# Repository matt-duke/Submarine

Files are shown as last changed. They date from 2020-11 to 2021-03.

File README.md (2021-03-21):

# Underwater ROV

## Motivation
The inspiration for this project was born on a sunny summer day on Skeleton Lake in Ontario, Canada. This lake is thought to be formed by a meteorite impact about 800 million years ago, followed by several periods of glaciation. This origin story, combined with the lake's crystal clear spring fed water, has resulted in clearly visible incredible underwater topography. However, only a very small portion can be seen from the waters surface, leaving acres of interesting glacial aftermath, submarine rock cliffs and (possibly) optimistic plant life hidden from view and left to the imagination.

<figure>
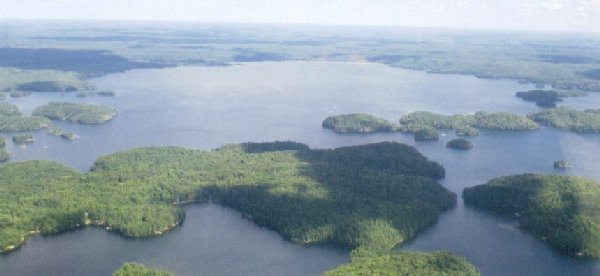
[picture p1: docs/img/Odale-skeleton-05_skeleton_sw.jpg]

<figcaption><p align=center>Aerial view of the west side of Skeleton Lake</p></figcaption>
</figure>

The intent of this project has been part practical outcome and part learning experience. So far, the learning portion has been extremely valuable, with many iterations, over-complications and replacements. However, a working prototype is planned for the spring of 2021.

## System Overview
The ROV consists of 3 sperate processors with specific functions dedicated to each. The main processor card (MPC) inside the submarine handles high level monitoring and control tasks, including a database server. It is connected by a CAT5 link to the auxillary processor card (APC), which is on the water's surface and acts as the human to machine interface. This device is intended to receive user commands and send them to the MPC, while displaying critical information with minimal delay.
<figure>
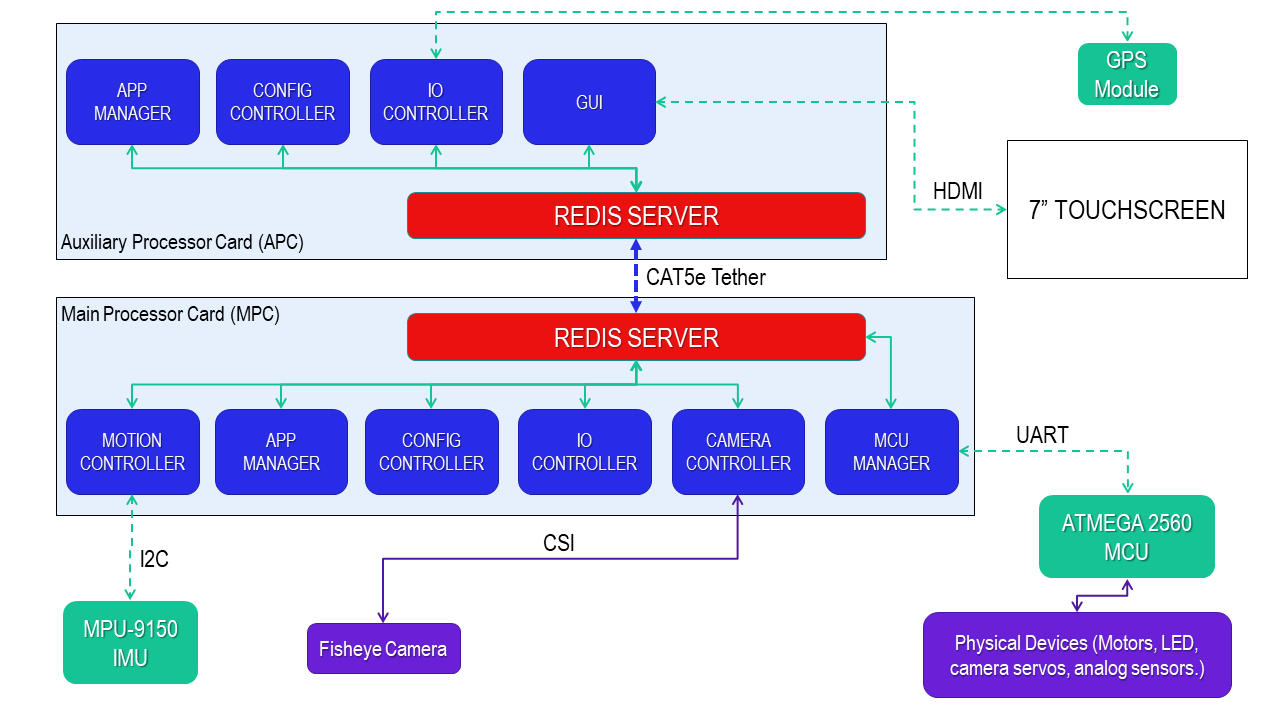
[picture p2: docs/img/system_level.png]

<figcaption><p align=center>System level block diagram</p></figcaption>
</figure>
Because low latency is critical in this application, inter-process communication is accomplished using a Redis server. It acts as an in memory variable cache, with the added ability to act as a message broker. The main redis server lives on the MPC inside the submarine, with a synchronized redis server on the APC acting as a forwarder.

### Hardware

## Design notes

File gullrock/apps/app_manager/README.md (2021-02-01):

# Application Manager

## Overview
This application starts and monitors other apps to watch for faults and crashes. It also starts thirdparty apps such as redis-server. As the main entrypoint for submarine software, it should be run at startup and launch applications in the correct sequence.

## Redis Details
Device code is either `mpc` or `apc`.
### Keys:
`<device_code>_app_manager:` Current app status
### Publishers:
N/A
### Subscriptions:
`<device_code>_app_manager.transition`: Request transition to given state ID
## Requirements
```
    logger
    hiredis
    pthread
    event
    event_pthreads
```

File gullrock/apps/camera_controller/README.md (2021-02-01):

# Camera Controller

## Overview
This application handles camera specific functionality. It controls the RaspiCam and a gstream server to send video to the APC using IP level protocols. This method is the best I've found for low latency, high quality digital video streaming, and allows for a very fine level of control.

## Redis Details
Device code is either `mpc` or `apc`.
### Keys:
`<device_code>_camera_controller`: Current app status
`cam_status`: Output of vcgencmd camera status (supported and detected)
### Publishers:
N/A
### Subscriptions:
`<device_code>_camera_controller.transition`: Request transition to given state ID
`start_camera_server`: Initialize camera server (gstream) to send video to APC
`stop_camera_server`: Stop camera stream
## Requirements
```
    logger
    hiredis
    pthread
    event
    event_pthreads
```

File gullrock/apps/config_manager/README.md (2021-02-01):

# Config Manager

## Overview
This application is used to detect software validity and iniiliaze common variables from configuration files. It is heavily involved in the firmware update procedure by reading app CRC values and comparing to expected values. This feature is less critical for development and can be disabled or ignored.

## Redis Details
Device code is either `mpc` or `apc`.
### Keys:
`<device_code>_config_manager`: Current app status
### Publishers:
N/A
### Subscriptions:
`<device_code>_config_manager.transition`: Request transition to given state ID
## Requirements
```
    logger
    hiredis
    pthread
    event
    event_pthreads
```

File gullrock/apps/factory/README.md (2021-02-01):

# Factory

## Overview
Apps for use by the "factory" (me) and not for use on "production" hardware. Examples include sensor calibration apps that need to be run on target hardware.

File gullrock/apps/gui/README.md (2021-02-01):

## GUI Interface

## Overview
This Python based GUI is meant to be used from a device on the water's surface, connected by ethernet tether to the ROV. It is designed to be used on the APC, which is a Raspberry Pi touchscreen tablet meant to act as a cheap, portable and replacable alternative to and laptop or tablet.

This GUi is relatively simple and has 3 tasks:
- Read and display data from a Redis database
- Send commands to the ROV using Redis PUBSUB
- Display video by connecting to the GStream server

GUI input is meant to come from a touchscreen or (preferably) an off-the-shelf USB game controller.

## Redis Details
### Keys:
`qt5_gui_status`: Current app status
### Publishers:
`set.io.m1_speed`
`set.io.m2_speed`
`set.io.cam_pitch`
`set.io.cam_yaw`
`set.io.headlight`
### Subscriptions:
`mcu_refresh`: ? Uncertain whether to use polling or notifications for GUI refresh
## Requirements
`python3-gi python3-gi-cairo gir1.2-gtk-3.0`: PyGObject support on Debian based distro
See requirements.txt for PIP packages

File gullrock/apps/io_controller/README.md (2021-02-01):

# IO Controller

## Overview
Manages all functionality regarding the MPC or APc and its physical surroudnings or hardware status. Used mainly for gathering and updating the Redis database with sensor data, including CPU temperature and IMU sensor results.

The main loop in this app should be very fast to minimize data lag.

## Redis Details
Device code is either `mpc` or `apc`.
### Keys:
`<device_code>_io_controller`: Current app status
`accel_x`: X-wise acceleration
`accel_y`: Y-wise acceleration
`accel_z`: Z-wise acceleration (including gravity)
`<device_code>_cpu_temp`: vcgencmd reported CPU temperature
`<device_code>_volts`: vcgencmd reported core voltage
`<device_code>_cpu_idle`: CPU idle time since last startup
`<device_code>_load_avg_1min`: CPU load avg over previous 1min (total, not per core)
`<device_code>_load_avg_5min`: CPU load avg over previous 5min (total, not per core)
`<device_code>_load_avg_15min`: CPU load avg over previous 15min (total, not per core)
`<device_code>_under_volt`: vcgencmd CPU undervolt detected
`<device_code>_freq_cap`: vcgencmd CPU frequency capped
`<device_code>_throttled`: vcgencmd CPU currently throttled
`<device_code>_soft_temp_limit`: vcgencmd CPU soft temp limit reached
### Publishers:
N/A
### Subscriptions:
`<device_code>_io_controller.transition`: Request transition to given state ID
## Requirements
```
    logger
    hiredis
    pthread
    event
    event_pthreads
    mpu9150
```

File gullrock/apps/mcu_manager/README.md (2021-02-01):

# MCU Manager

## Overview
The MCU manager acts as a bridge between the Rasberry Pi based MPC and the ATmega2560 based MCU. A serial connection between the two devices uses the HDLC message format to form data packets, which includes start and stop bytes plus a CRC embeded in the payload. To simplify the protocol, the MCU acts as a slave, and only responds to messages following a request for data from the MPC. 
This app needs relatively high speed to update the Redis server in near real-time.

## Redis Details
Device code is either `mpc` or `apc`.
### Keys:
`<device_code>_mcu_manager`: Current app status
`m1_speed`: Left motor speed (0-255)
`m2_speed`: Right motor speed (0-255)
`m1_curr`: Left motor current in volts
`m2_curr`: Right motor current in volts
`mcu_state`: Internal state reported by MCU firmware
`water temp`: Submarine water temperature (sensor onboard)
`total_current`: Total current draw from submarine batteries
### Publishers:
N/A
### Subscriptions:
`<device_code>_mcu_manager.transition`: Request transition to given state ID
`set.io.*`: Listens to requests to set MCU settings such as `m1_speed` or `cam_yaw`

## Requirements
```
    logger
    hiredis
    pthread
    event
    event_pthreads
    serialport
    minihdlc
```

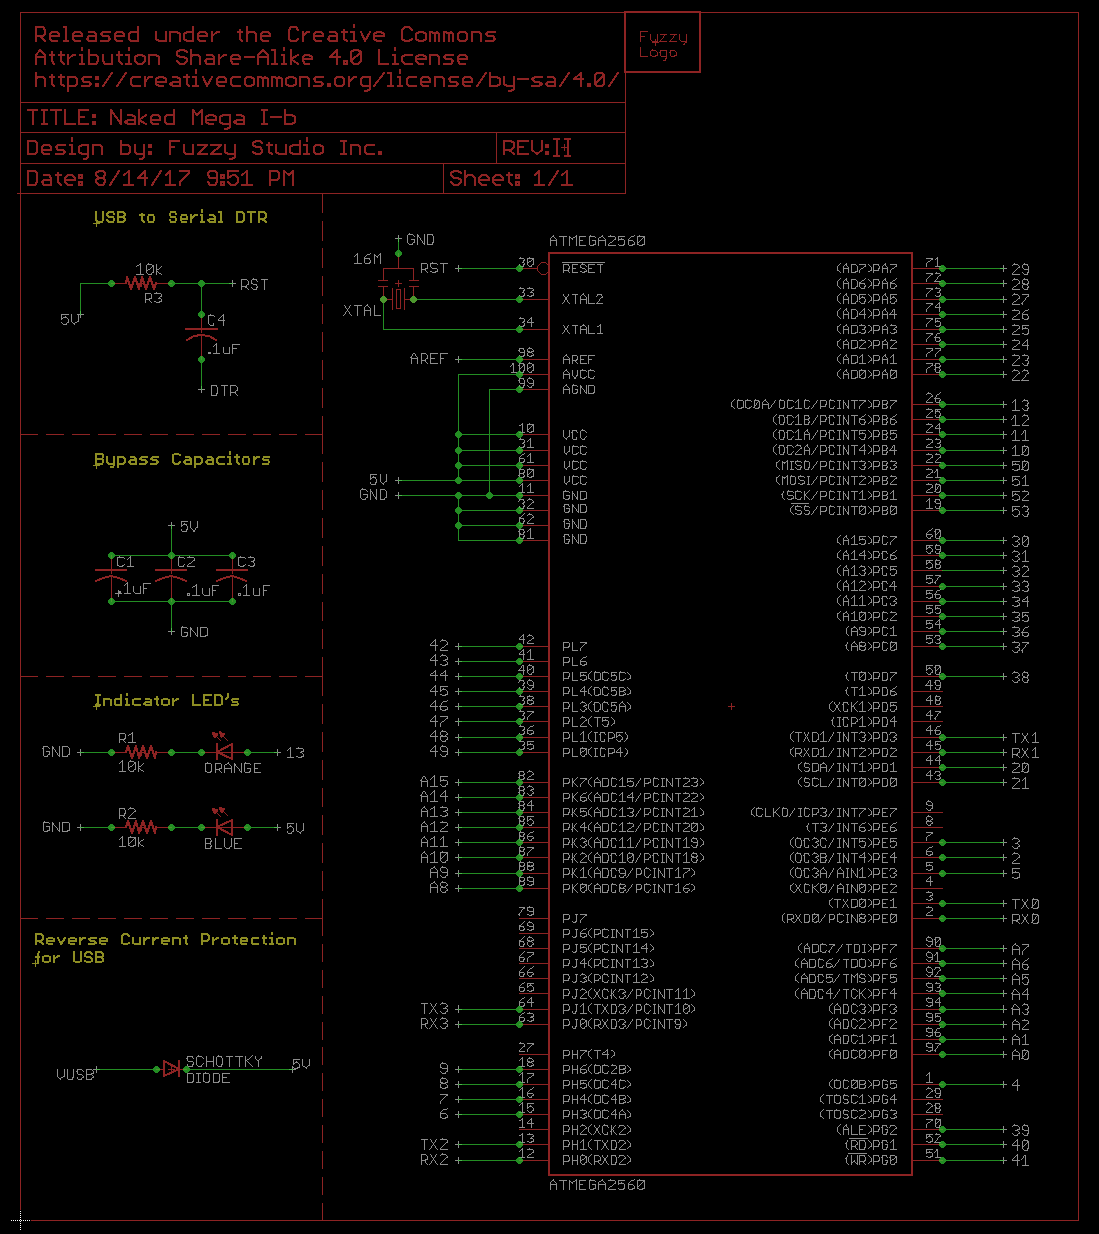
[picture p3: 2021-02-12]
CAD/MPC/Fuzzy-Naked-Mega-master/Revision I-b/Schematic.png

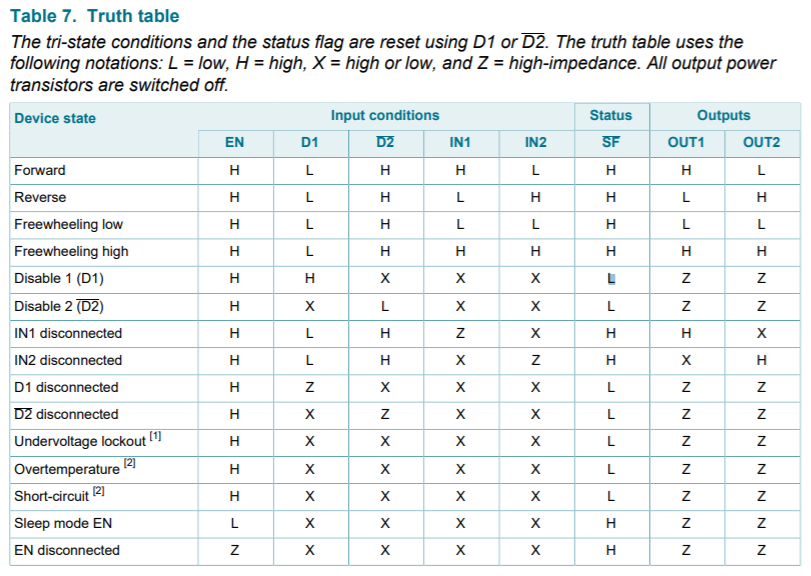
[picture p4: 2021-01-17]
docs/MC33926 truth table.PNG

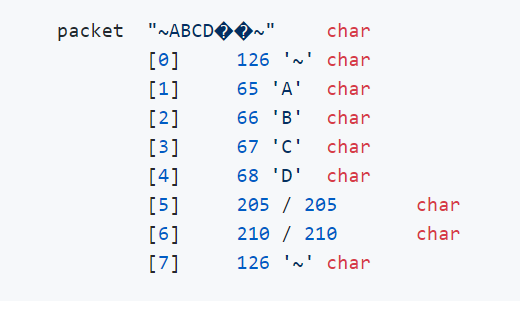
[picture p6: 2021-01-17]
docs/packet framing hdlc.PNG

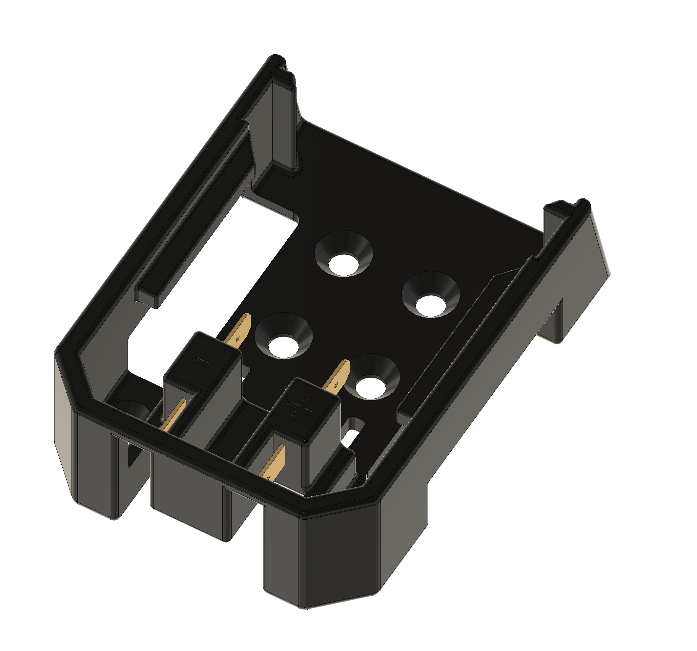
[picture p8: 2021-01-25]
CAD/V3/milwaukee-m18-battery-adapter-connector-dock-holder-mount-injection-molded-1.snapshot.3/Screen Shot 2020-12-06 at 12.32.36 PM.png

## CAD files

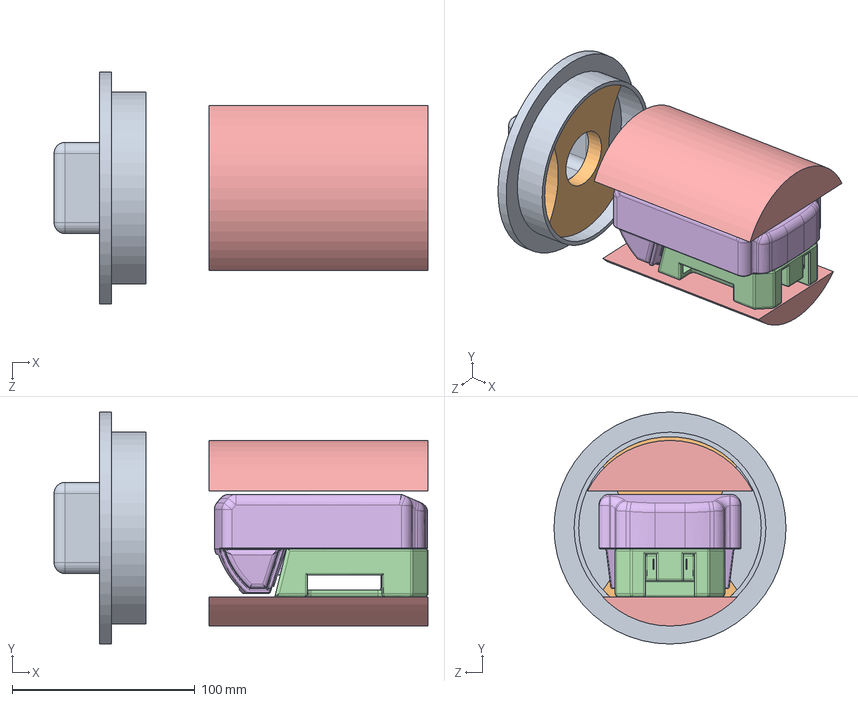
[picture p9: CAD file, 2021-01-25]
CAD/V3/Assem1.SLDASM
204.8 x 127.0 x 127.0 mm
Frame.step
battery_adaptor_mount
Milwaukee M18 Red Lithium Battery.step

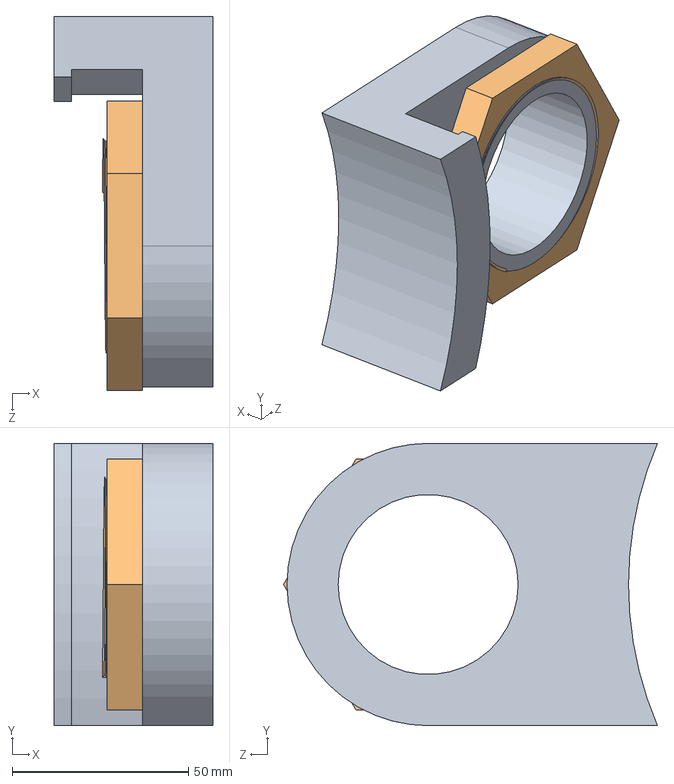
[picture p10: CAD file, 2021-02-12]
CAD/assem_led.SLDASM
45.0 x 80.0 x 106.0 mm
led_mount
bolt

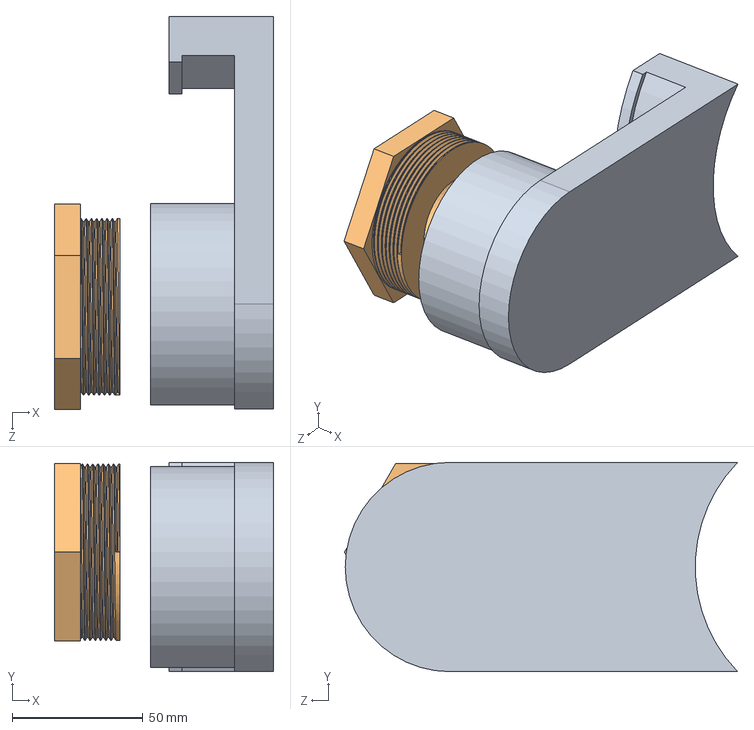
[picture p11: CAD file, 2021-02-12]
CAD/assem_motor.SLDASM
83.7 x 80.0 x 150.3 mm
motor_mount
bolt_motor

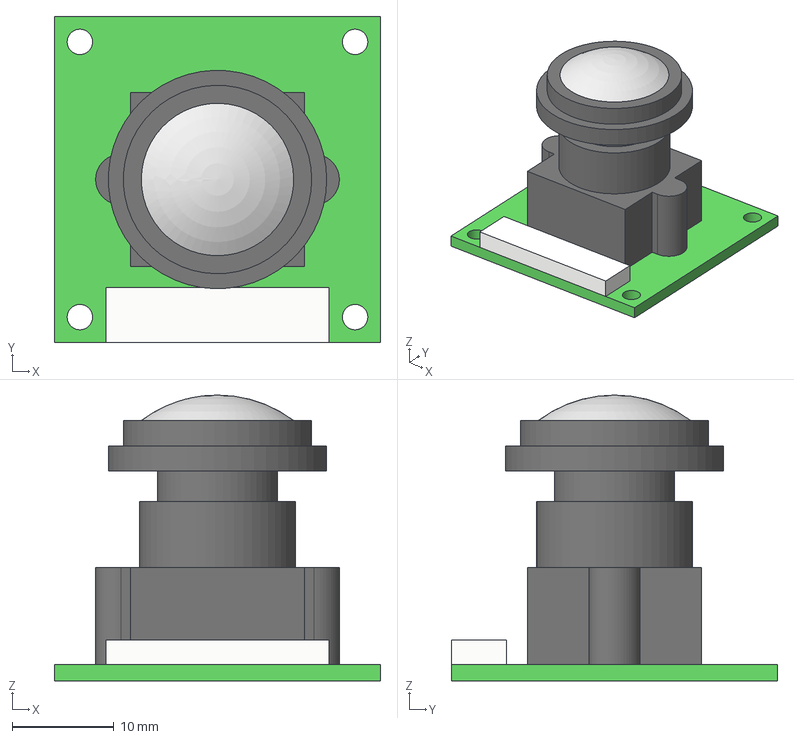
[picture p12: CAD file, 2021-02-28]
CAD/PiCam_WideAngle v2.step
32.1 x 32.1 x 28.2 mm
Lens
Connector
Lense frame
PCB
Camera Body

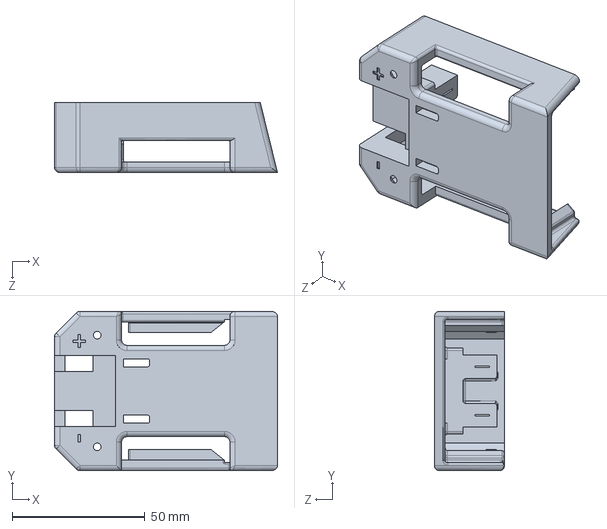
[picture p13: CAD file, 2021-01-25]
CAD/V3/battery_mount_2.SLDPRT
83.9 x 60.0 x 26.4 mm

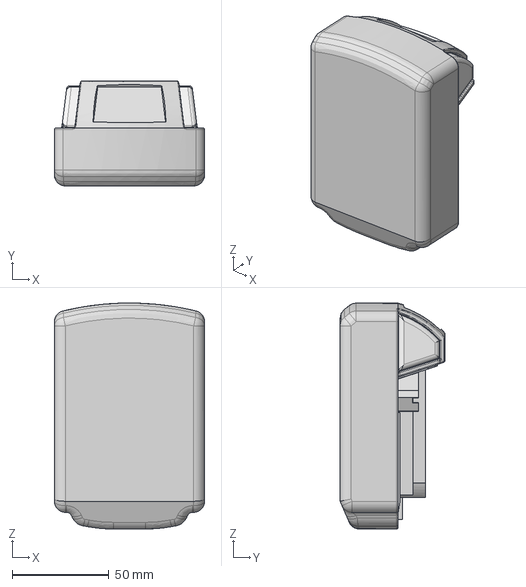
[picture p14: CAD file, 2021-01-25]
CAD/V3/milwaukee-m18-battery-1.snapshot.3/Milwaukee M18 Red Lithium Battery.step
77.7 x 54.2 x 116.8 mm

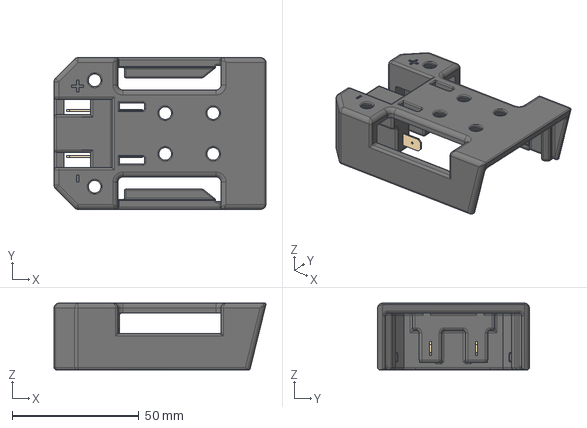
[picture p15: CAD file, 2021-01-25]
CAD/V3/milwaukee-m18-battery-adapter-connector-dock-holder-mount-injection-molded-1.snapshot.3/M18 battery mount.step
83.7 x 60.0 x 26.4 mm
Contacts
Frame

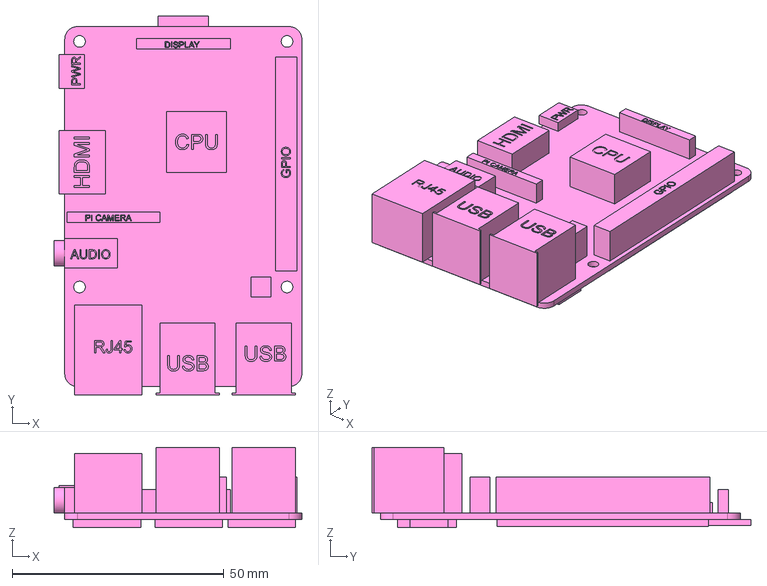
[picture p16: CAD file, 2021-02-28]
CAD/Raspberry pi 3B+ model v10.step
58.5 x 89.5 x 19.0 mm

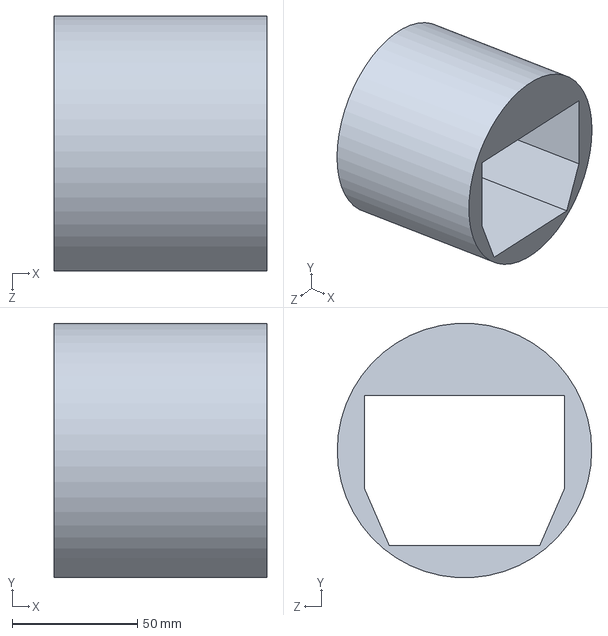
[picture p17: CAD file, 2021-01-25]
CAD/V3/battery_adaptor_mount.SLDPRT
85.0 x 101.4 x 101.6 mm

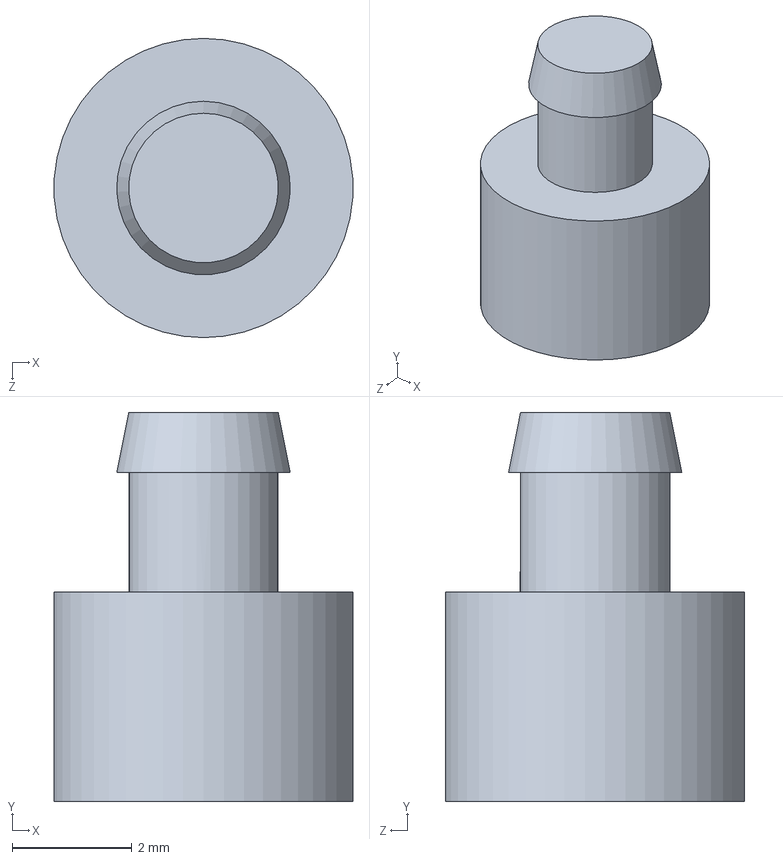
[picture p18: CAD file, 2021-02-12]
CAD/spacer_board.SLDPRT
4.99 x 6.50 x 5.00 mm

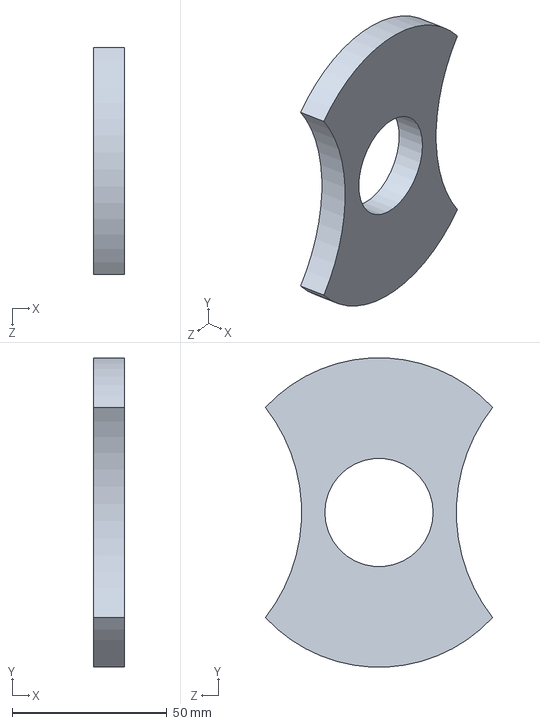
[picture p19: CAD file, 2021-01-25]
CAD/V3/PLA_cap_insert.SLDPRT
10.0 x 99.9 x 73.4 mm

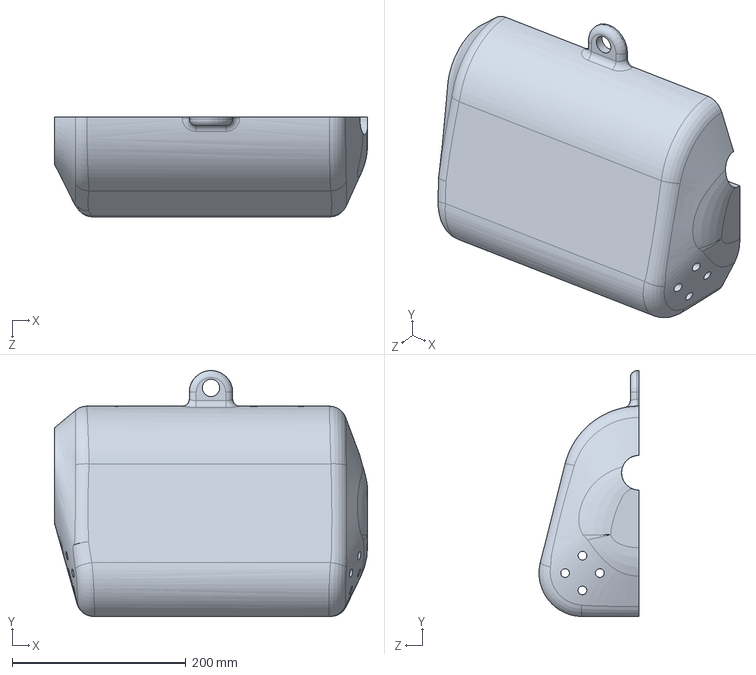
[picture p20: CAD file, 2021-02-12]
CAD/sub3.SLDPRT
360.0 x 283.0 x 115.0 mm

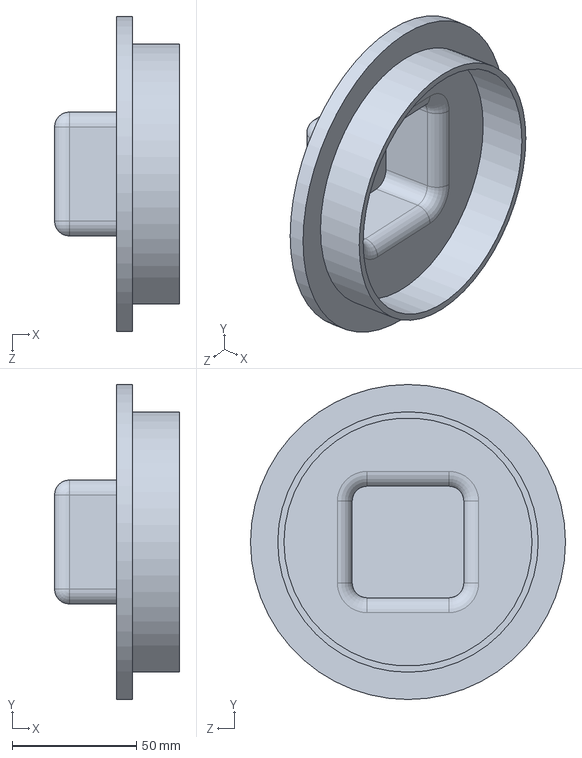
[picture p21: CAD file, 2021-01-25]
CAD/V3/4in_ABS_cap.SLDPRT
50.4 x 127.0 x 127.0 mm

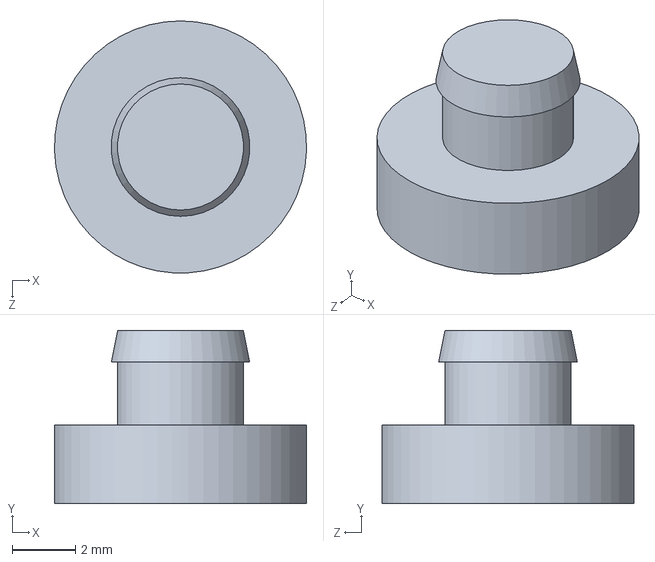
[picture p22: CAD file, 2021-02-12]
CAD/spacer_front.SLDPRT
8.00 x 5.50 x 8.00 mm

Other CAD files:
CAD/spacer_rpi.SLDPRT
CAD/spacer_motor.SLDPRT
CAD/sub_final.SLDPRT
CAD/mount template.SLDPRT
CAD/V3/milwaukee-m18-battery-1.snapshot.3/Milwaukee M18 Red Lithium battery.f3d
CAD/V3/milwaukee-m18-battery-adapter-connector-dock-holder-mount-injection-molded-1.snapshot.3/M18 battery mount.SLDPRT
CAD/board_standoff.SLDPRT
CAD/bolt.SLDPRT
CAD/bolt_led.SLDPRT
CAD/bolt_motor.SLDPRT
CAD/cam_mount.SLDPRT
CAD/controller.SLDPRT
CAD/controller_rounded.SLDPRT
CAD/led_mount.SLDPRT
CAD/light_mount.SLDPRT
CAD/motor_mount.SLDPRT
CAD/mount.SLDPRT
CAD/part_mount_template.SLDPRT
CAD/servo_mnt_2.SLDPRT
CAD/spacer_ard.SLDPRT
CAD/spacer_ethernet.SLDPRT
CAD/sub1.SLDPRT
CAD/sub2.SLDPRT

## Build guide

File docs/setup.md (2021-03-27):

# Building
## Cross Compiling
http://amgaera.github.io/blog/2014/04/10/cross-compiling-for-raspberry-pi-on-64-bit-linux/
https://stackoverflow.com/questions/19162072/how-to-install-the-raspberry-pi-cross-compiler-on-my-linux-host-machine/58559140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
https://stackoverflow.com/questions/5971921/building-a-library-using-autotools-from-cmake
https://stackoverflow.com/questions/19162072/how-to-install-the-raspberry-pi-cross-compiler-on-my-linux-host-machine
https://stackoverflow.com/questions/33559884/fatal-error-bits-types-h-file-not-found
https://stackoverflow.com/questions/11471722/libstdc-so-6-cannot-open-shared-object-file-no-such-file-or-directory

autoreconf
libtool
gcc
g++

## Generating image for Raspberry Pi
https://github.com/zeromq/czmq/tree/master/builds/rpi

# Dependecies
## GSTREAMER
gir1.2-gst-plugins-base-1.0 -- for GstVideo (not needed?)

gstreamer1.0-libav

## REDIS
wget http://download.redis.io/redis-stable.tar.gz
tar xvzf redis-stable.tar.gz
cd redis-stable
make

git clone git://git.drogon.net/wiringPi
$ cd wiringPi
$ ./build

## REDIS C LIBRARY
hiredis-vip
make -> generates libhiredis_vip.so
copy to /usr/lib
update using sudo ldconfig
check with sudo ldconfig -p | grep redis

## SERIAL LIBRARY
git clone https://github.com/sigrokproject/libserialport.git
install dh-autoreconf
run autogen.sh, then configure.sh
make install
ldconfig

## GST_RPICAM
#https://github.com/thaytan/gst-rpicamsrc/
sudo apt install libgstreamer1.0-dev libgstreamer-plugins-base1.0-dev
git clone https://github.com/thaytan/gst-rpicamsrc.git
cd gst-rpicamsrc
./autogen.sh
make
sudo make install

## Disable BT to use UART (PL011)
https://scribles.net/disabling-bluetooth-on-raspberry-pi/
https://www.raspberrypi.org/documentation/configuration/uart.md

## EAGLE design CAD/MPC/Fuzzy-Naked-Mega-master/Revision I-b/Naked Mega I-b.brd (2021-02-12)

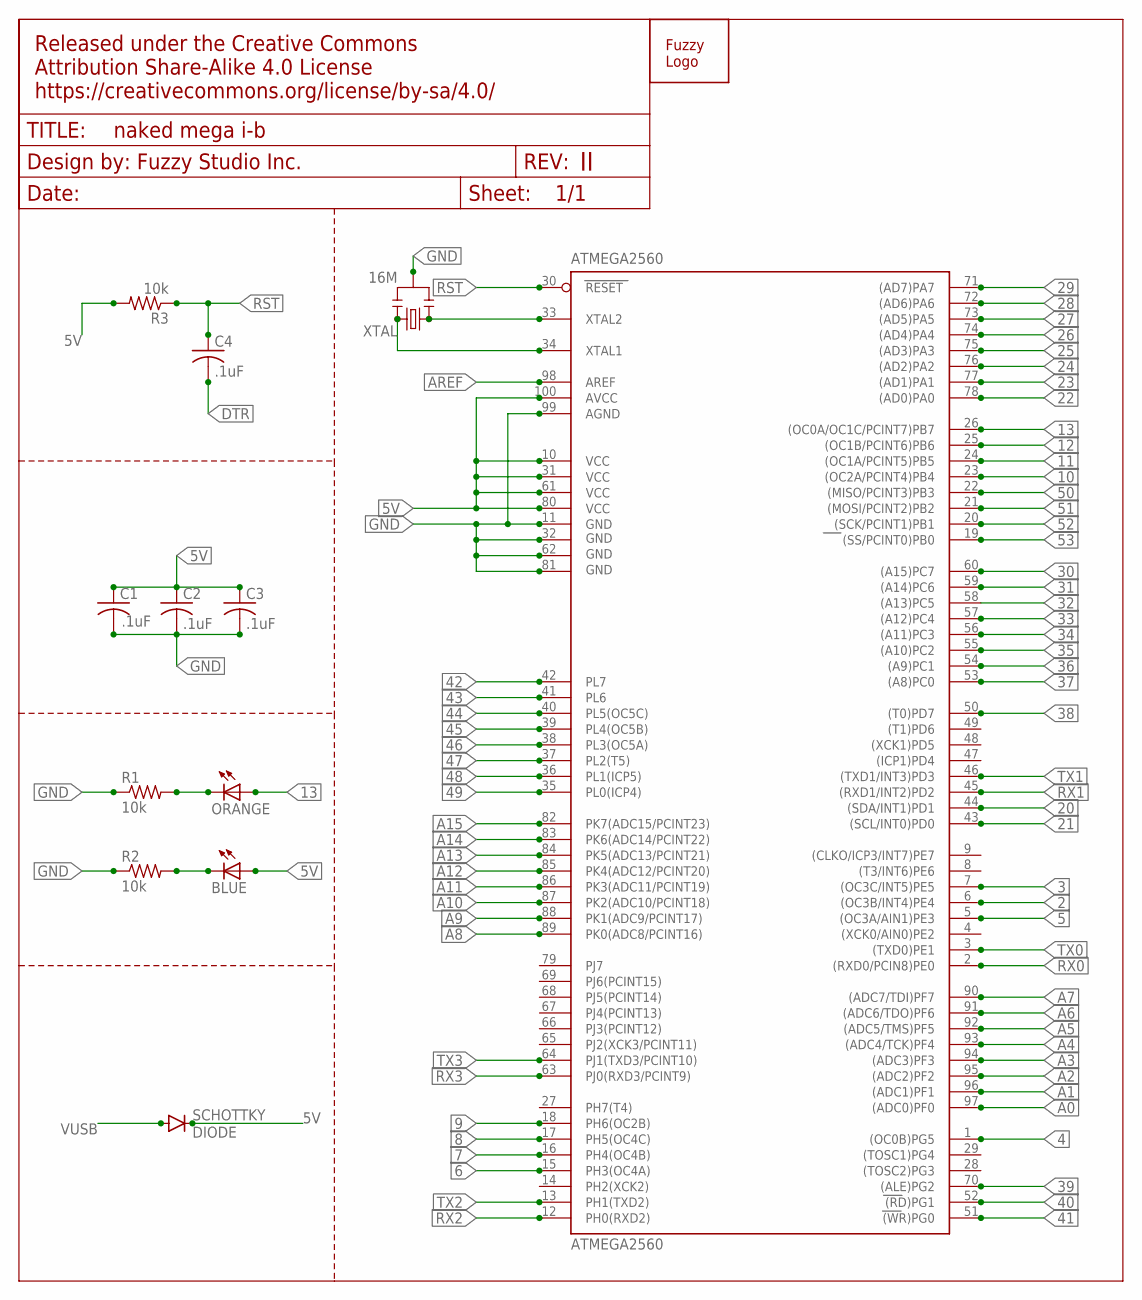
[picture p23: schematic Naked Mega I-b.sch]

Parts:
ATMEGA2560: ATMEGA2560; TQFP100
BLUE: L; SMD-0805-LED
C1: CAPACITOR-SMD-0805; SMD-0805
C2, C3, C4: .1uF; SMD-0805
ORANGE: L; SMD-0805-LED
R1, R2, R3: 10k; SMD-0805
SCHOTTKY: DIODE; SOD-323
U$1: LOGO; LOGO-S
U$3: DOCFRAME; CREATIVECOMMONS
XTAL: 16M; RESONATOR

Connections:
2: ATMEGA2560.6 ((OC3B/INT4)PE4)
3: ATMEGA2560.7 ((OC3C/INT5)PE5)
4: ATMEGA2560.1 ((OC0B)PG5)
5: ATMEGA2560.5 ((OC3A/AIN1)PE3)
5V: ATMEGA2560.10 (VCC), ATMEGA2560.31 (VCC1), ATMEGA2560.61 (VCC2), ATMEGA2560.80 (VCC3), ATMEGA2560.100 (AVCC), BLUE.1 (A), C1.1, C2.1, C3.1, R3.2, SCHOTTKY.C
6: ATMEGA2560.15 (PH3(OC4A))
7: ATMEGA2560.16 (PH4(OC4B))
8: ATMEGA2560.17 (PH5(OC4C))
9: ATMEGA2560.18 (PH6(OC2B))
10: ATMEGA2560.23 ((OC2A/PCINT4)PB4)
11: ATMEGA2560.24 ((OC1A/PCINT5)PB5)
12: ATMEGA2560.25 ((OC1B/PCINT6)PB6)
13: ATMEGA2560.26 ((OC0A/OC1C/PCINT7)PB7), ORANGE.1 (A)
20: ATMEGA2560.44 ((SDA/INT1)PD1)
21: ATMEGA2560.43 ((SCL/INT0)PD0)
22: ATMEGA2560.78 ((AD0)PA0)
23: ATMEGA2560.77 ((AD1)PA1)
24: ATMEGA2560.76 ((AD2)PA2)
25: ATMEGA2560.75 ((AD3)PA3)
26: ATMEGA2560.74 ((AD4)PA4)
27: ATMEGA2560.73 ((AD5)PA5)
28: ATMEGA2560.72 ((AD6)PA6)
29: ATMEGA2560.71 ((AD7)PA7)
30: ATMEGA2560.60 ((A15)PC7)
31: ATMEGA2560.59 ((A14)PC6)
32: ATMEGA2560.58 ((A13)PC5)
33: ATMEGA2560.57 ((A12)PC4)
34: ATMEGA2560.56 ((A11)PC3)
35: ATMEGA2560.55 ((A10)PC2)
36: ATMEGA2560.54 ((A9)PC1)
37: ATMEGA2560.53 ((A8)PC0)
38: ATMEGA2560.50 ((T0)PD7)
39: ATMEGA2560.70 ((ALE)PG2)
40: ATMEGA2560.52 ((RD)PG1)
41: ATMEGA2560.51 ((WR)PG0)
42: ATMEGA2560.42 (PL7)
43: ATMEGA2560.41 (PL6)
44: ATMEGA2560.40 (PL5(OC5C))
45: ATMEGA2560.39 (PL4(OC5B))
46: ATMEGA2560.38 (PL3(OC5A))
47: ATMEGA2560.37 (PL2(T5))
48: ATMEGA2560.36 (PL1(ICP5))
49: ATMEGA2560.35 (PL0(ICP4))
50: ATMEGA2560.22 ((MISO/PCINT3)PB3)
51: ATMEGA2560.21 ((MOSI/PCINT2)PB2)
52: ATMEGA2560.20 ((SCK/PCINT1)PB1)
53: ATMEGA2560.19 ((SS/PCINT0)PB0)
A0: ATMEGA2560.97 ((ADC0)PF0)
A1: ATMEGA2560.96 ((ADC1)PF1)
A2: ATMEGA2560.95 ((ADC2)PF2)
A3: ATMEGA2560.94 ((ADC3)PF3)
A4: ATMEGA2560.93 ((ADC4/TCK)PF4)
A5: ATMEGA2560.92 ((ADC5/TMS)PF5)
A6: ATMEGA2560.91 ((ADC6/TDO)PF6)
A7: ATMEGA2560.90 ((ADC7/TDI)PF7)
A8: ATMEGA2560.89 (PK0(ADC8/PCINT16))
A9: ATMEGA2560.88 (PK1(ADC9/PCINT17))
A10: ATMEGA2560.87 (PK2(ADC10/PCINT18))
A11: ATMEGA2560.86 (PK3(ADC11/PCINT19))
A12: ATMEGA2560.85 (PK4(ADC12/PCINT20))
A13: ATMEGA2560.84 (PK5(ADC13/PCINT21))
A14: ATMEGA2560.83 (PK6(ADC14/PCINT22))
A15: ATMEGA2560.82 (PK7(ADC15/PCINT23))
AREF: ATMEGA2560.98 (AREF)
DTR: C4.2
GND: ATMEGA2560.11 (GND), ATMEGA2560.32 (GND1), ATMEGA2560.62 (GND2), ATMEGA2560.81 (GND3), ATMEGA2560.99 (AGND), C1.2, C2.2, C3.2, R1.1, R2.1, XTAL.2
unnamed: ATMEGA2560.34 (XTAL1), XTAL.3
unnamed: ATMEGA2560.33 (XTAL2), XTAL.1
unnamed: ORANGE.2 (C), R1.2
unnamed: BLUE.2 (C), R2.2
RST: ATMEGA2560.30 (RESET), C4.1, R3.1
RX0: ATMEGA2560.2 ((RXD0/PCIN8)PE0)
RX1: ATMEGA2560.45 ((RXD1/INT2)PD2)
RX2: ATMEGA2560.12 (PH0(RXD2))
RX3: ATMEGA2560.63 (PJ0(RXD3/PCINT9))
TX0: ATMEGA2560.3 ((TXD0)PE1)
TX1: ATMEGA2560.46 ((TXD1/INT3)PD3)
TX2: ATMEGA2560.13 (PH1(TXD2))
TX3: ATMEGA2560.64 (PJ1(TXD3/PCINT10))
VUSB: SCHOTTKY.A

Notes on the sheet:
.1uF

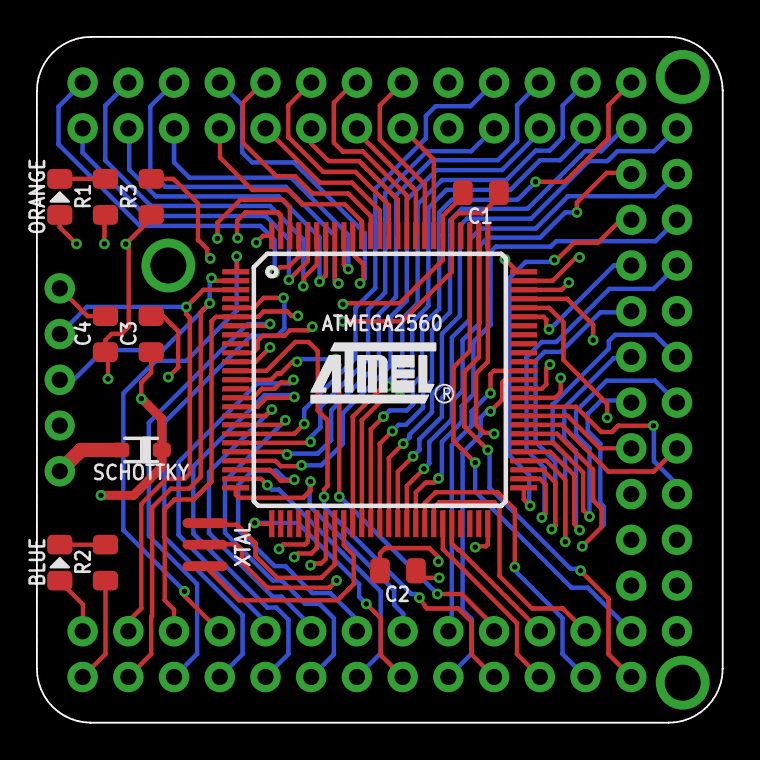
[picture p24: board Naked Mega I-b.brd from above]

Board: 4 copper layers, 38.1 x 38.1 mm, 14 parts (1 on the bottom side), 8 nets.

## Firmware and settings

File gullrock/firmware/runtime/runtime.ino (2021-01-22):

#include <Arduino_FreeRTOS.h>
#include <Adafruit_NeoPixel.h>
#include <Arduhdlc.h>
#include <hdlc_def.h>

#include "command_handler.h"
#include "def.h"

// Functions
void send_character(uint8_t data);
void hdlc_frame_handler(const uint8_t *data, uint16_t length);

packet_t GlobalBuffer = {};

Adafruit_NeoPixel status(1, LED_STATUS, NEO_RGB + NEO_KHZ800);
Arduhdlc hdlc(&send_character, &hdlc_frame_handler, MAX_HDLC_FRAME_LENGTH);

// Function prototypes
void send_character(uint8_t data);
void hdlc_frame_handler(const uint8_t *data, uint16_t length);

void TaskReadSerial(void *pvParameters);
void TaskReadSensors(void *pvParameters);
void TaskStatus(void *pvParameters);
void TaskNetwork(void *pvParameters);
void TaskCamera(void *pvParameters);
void TaskWatchdog(void *pvParameters);

void setup() {
    GlobalState = MCU_STATE_INIT;

    //Turn off status LED
    status.setPixelColor(0, 0, 0, 0);
    status.show();

    //Pin modes
    pinMode(LED_BUILTIN, OUTPUT);
    pinMode(LED_STATUS, OUTPUT);
    //pinMode(LED_ETH, OUTPUT);
    pinMode(CURR_PIN, INPUT);
    //Serial
    SERIAL_DEBUG.begin(9600);
    SERIAL_DEBUG.println("Running setup.");
    SERIAL.begin(PORT_SPEED);
    while (!SERIAL);  //Wait for serial to become available

    status.setPixelColor(0, 0, 0, 0);
    status.show();
    setup_external();

    //FREE_RTOS
    xTaskCreate(TaskStatus, "TaskStatus", 128, NULL, 2, &TaskStatus_handle);
    //xTaskCreate(TaskNetwork, "TaskNetwork", 128, NULL, 2, &TaskNetwork_handle);
    //xTaskCreate(TaskCamera, "TaskCamera", 128, NULL, 2, &TaskCamera_handle);
    xTaskCreate(TaskReadSensors, "TaskReadSensors", 128, NULL, 2, &TaskReadSensors_handle);
    xTaskCreate(TaskReadSerial, "TaskReadSerial", 250, NULL, 1, &TaskReadSerial_handle);
    xTaskCreate(TaskWatchdog, "TaskWatchdog", 128, NULL, 1, &TaskWatchdog_handle);

    vTaskStartScheduler();
}

void loop() {}

void TaskPOST(void *pvParameters) {
    static uint32_t thread_notification;

    for (;;) {
        thread_notification = ulTaskNotifyTake(pdTRUE, portMAX_DELAY);
        if (thread_notification) {
            SERIAL_DEBUG.println("TEST MODE STARTED");
            GlobalState = MCU_STATE_POST;
            if (test_mode()) {
                GlobalState = MCU_STATE_READY;
            } else {
                GlobalState = MCU_STATE_FAULT;
            }
            SERIAL_DEBUG.println("TEST MODE ENDED");
        }
    }
}

void TaskWatchdog(void *pvParameters) {
    const int min_stack_size = 50;
    const int num_tasks = 4;
    const TaskHandle_t *tasks[num_tasks] = {&TaskStatus_handle, &TaskReadSensors_handle, &TaskReadSerial_handle, &TaskWatchdog_handle};
    const char *task_names[num_tasks] = {"TaskStatus_handle", "TaskReadSensors_handle", "TaskReadSerial_handle", "TaskWatchdog_handle"};
    for (;;) {
        for (int i=0; i<num_tasks;i++) {
            uint32_t hwm = uxTaskGetStackHighWaterMark(*tasks[i]);
            if (hwm < min_stack_size) {
                SERIAL_DEBUG.print("WARNING: Low free stack in ");
                SERIAL_DEBUG.println(task_names[i]);
            }
        }

        bool fault = false;
        if (MotorDriver.getM1Fault()) {
            SERIAL_DEBUG.println("M1 Fault");
        }
        if (MotorDriver.getM2Fault()) {
            SERIAL_DEBUG.println("M2 Fault");
        }
        if (fault) {
            fault_handler();
        }
        vTaskDelay(100 / portTICK_PERIOD_MS);
    }
}

void TaskReadSerial(void *pvParameters) {
    for (;;) {
        if (SERIAL.available() > 0) {
        } else {
            continue;
        }
        while (SERIAL.available() > 0) {
            uint8_t rx = (uint8_t)SERIAL.read();
            //SERIAL_DEBUG.print("Received: ");
            //SERIAL_DEBUG.println(rx, DEC);
            hdlc.charReceiver(rx);
        }
        //SERIAL_DEBUG.println("Done reading...");
        vTaskDelay(1);
    }
}

void TaskReadSensors(void *pvParameters) {
    for (;;) {
        TotalCurrent.read();
        M1Current.read();
        M2Current.read();
        SERIAL_DEBUG.println("Reading sensors");
        vTaskDelay(1000 / portTICK_PERIOD_MS);  //delay 1000 ms
    }
}

void TaskStatus(void *pvParameters) {
    int strobe = 0;
    bool add = true;
    colour_t ColourProfiles[MCU_NUM_STATES];
    ColourProfiles[MCU_STATE_INIT] = (colour_t){20, 0, 80, 50};
    ColourProfiles[MCU_STATE_FAULT] = (colour_t){100, 0, 0, 40};
    ColourProfiles[MCU_STATE_POST] = (colour_t){60, 0, 85, 25};
    ColourProfiles[MCU_STATE_READY] = (colour_t){0, 100, 20, 0};
    colour_t c;

    for (;;) {
        c = ColourProfiles[GlobalState];
        SERIAL_DEBUG.println("Update status LED");
        if (c.rate != 0) {
            float mult = float(strobe) / 100;
            status.setPixelColor(0, c.r * mult, c.g * mult, c.b * mult);
            if (strobe >= 100) {
                add = false;
            } else if (strobe <= 0) {
                add = true;
            }
            if (add) {
                strobe += 1;
            } else {
                strobe -= 1;
            }
        } else {
            status.setPixelColor(0, c.r, c.g, c.b);
        }
        status.show();
        int rate = 1000;
        vTaskDelay(1000 / portTICK_PERIOD_MS);
    }
}

void TaskNetwork(void *pvParameters) {
    uint8_t i = 0;
    bool add = true;
    int rate = 1000;
    for (;;) {
        if (!NetworkStatus.layer1) {
            i++;
        } else if (!NetworkStatus.apc) {
            // strobe effect
            if (i == 255 || i == 0) add = !add;
            (add) ? i++ : i--;
        } else if (NetworkStatus.wan) {
            i = 255;
        }
        analogWrite(LED_ETH, i);
        vTaskDelay(rate / portTICK_PERIOD_MS);
    }
}

void TaskCamera(void *pvParameters) {
    for (;;) {
        if (!CamCtrl.on_target()) {
            SERIAL_DEBUG.println("Updating camera...");
            while (!CamCtrl.on_target()) {
                CamCtrl.update();
                vTaskDelay(1);
            }
            SERIAL_DEBUG.println("Finished updating camera.");
        }
        vTaskDelay(10 / portTICK_PERIOD_MS);  // delay 10 ms
    }
}

//Function to send out one 8bit character
void send_character(uint8_t data) {
    SERIAL.print((char)data);
}

//Frame handler function. What to do with received data?
void hdlc_frame_handler(const uint8_t *data, uint16_t length) {
    if (length != PACKET_SIZE) {
        SERIAL_DEBUG.println("Improper packet size.");
        return;
    }
    packet_t in_p = {};
    packet_t out_p = {};
    for (int i = 0; i < length; i++) {
        in_p.ui8[i] = data[i];
    }
    free(data);
    out_p.s.id = in_p.s.id;
    command_handler(&in_p, &out_p);
    hdlc.sendFrame((uint8_t *)&out_p.ui8, sizeof(out_p.ui8));
    SERIAL_DEBUG.println("SENT");
}

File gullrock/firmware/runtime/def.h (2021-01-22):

#pragma once

#include <Arduino.h>
#include <hdlc_def.h>
#include <Arduino_FreeRTOS.h>
#include <semphr.h>
#include <CameraControl.h>
#include <MC33926Driver.h>
#include <Sensors.h>

// Function macros

#define SERIAL Serial
#define SERIAL_DEBUG Serial1

// Pin assignment
#define M1IN1 10
#define M1IN2 11
#define M1PWM 9
#define M1FB A7
#define M1SF 8
#define M2IN1 36
#define M2IN2 34
#define M2PWM 7
#define M2FB A6
#define M2SF 6
#define EN 32

#define AIN1 49
#define BIN1 40
#define AIN2 47
#define BIN2 42
#define PWMA 45
#define PWMB 44
#define STBY 51
#define EXP_LED_CURR 0.1

#define BTN_PIN 20
#define LED_ETH 21
#define LED_STATUS 4

#define CURR_PIN A15

#define SERVO_DELAY 25 //delay, higher=slower, ms
#define YAW_PIN 2
#define YAW_MAX 100
#define YAW_MIN 65
#define PITCH_PIN 3
#define PITCH_MAX 160
#define PITCH_MIN 90

struct colour_t {
  uint8_t r;
  uint8_t g;
  uint8_t b;
  uint16_t rate; //blink rate, ms
};

struct netstatus_t {
    bool layer1;
    bool apc;
    bool wan;
};

extern netstatus_t NetworkStatus;

extern TaskHandle_t TaskReadSerial_handle;
extern TaskHandle_t TaskReadSensors_handle;
extern TaskHandle_t TaskStatus_handle;
extern TaskHandle_t TaskNetwork_handle;
extern TaskHandle_t TaskCamera_handle;
extern TaskHandle_t TaskWatchdog_handle;

extern SemaphoreHandle_t interruptSemaphore; // For button press

extern uint8_t GlobalState;
extern data32_t last_post_result;

extern MC33926Driver MotorDriver;
extern CameraControl CamCtrl;

#define BUFFER_SIZE 10
extern Sensor TotalCurrent;
extern Sensor M1Current;
extern Sensor M2Current;

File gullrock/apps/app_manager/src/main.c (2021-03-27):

#include <stdio.h>
#include <stdlib.h>
#include <stdbool.h>
#include <string.h>

#include <hiredis.h>
#include <logger.h>

#include <common.h>
#include <baseapp.h>
#include <redis.h>

#define MAX_FAILURES 2

/* Variables */
extern const char *__progname;

#define APP_DIR "/apps"
#define START_REDIS "redis-server /persistent/redis.conf"

#define NUM_APPS 5
char* appNames[NUM_APPS] = {
  "camera_controller",
  "mcu_manager",
  "motion_controller",
  "io_controller",
  "config_controller"
};

/* Functions */
static void do_to_init();
static void do_post();
static void do_running();
static void do_test();

static int monitor_heartbeats(char *app_name);
static int start_app(char* app_name);
static int kill_app(char* app_name);

int main() {
  #ifdef TEST
  run_test(); 
  #else
  init_logging();
  app_transition_table[APP_STATE_INIT][APP_STATE_INIT] = do_to_init;
  app_run_table[APP_STATE_POST] = do_post;
  app_run_table[APP_STATE_RUNNING] = do_running;

  GlobalAppInit();

  while (1) {
    GlobalApp.run();
  }
  #endif
}

void do_to_init() {
  // TODO: Move starting redis server to startup script
  char buffer[128];
  if (run_cmd(START_REDIS, buffer, 128) != 0) {
    LOG_ERROR("Error starting redis server");
    GlobalApp.transition(APP_STATE_FAULT);
    return;
  } else {
    for (int i=0; i<NUM_APPS;i++) {
      start_app(appNames[i]);
    }
  }
}

void do_post() {
  bool any_in_post = false;
  bool any_in_fault = false;
  for (int i; i<NUM_APPS;i++) {
    int state = monitor_heartbeats(appNames[i]);
    if (state == APP_STATE_FAULT) {
      LOG_ERROR("%s in fault state.", appNames[i]);
      any_in_fault = true;
    } else if (state == APP_STATE_POST) {
      any_in_post = true;
    }
  }
  if (any_in_fault) {
    GlobalApp.transition(APP_STATE_FAULT); return;
  } else if (!any_in_post) {
    GlobalApp.transition(APP_STATE_RUNNING); return;
  }
}

void do_running() {
  bool any_in_fault = false;
  for (int i; i<NUM_APPS;i++) {
    int state = monitor_heartbeats(appNames[i]);
    if (state == APP_STATE_FAULT) {
      LOG_ERROR("%s in fault state.", appNames[i]);
      any_in_fault = true;
    }
  }
  if (any_in_fault) {
    GlobalApp.transition(APP_STATE_FAULT); return;
  }
}

int monitor_heartbeats(char *app_name) {
  redisReply *reply = redisCommand(GlobalApp.context,"TTL %s", app_name);
  if (reply->type != REDIS_REPLY_INTEGER) {
    LOG_ERROR("TTL error, reply is not an integer.");
    return -1;
  } else {
    switch (reply->integer) {
      case -2:
        LOG_ERROR("Heartbeat failed (expired): %s", app_name);
        return -1;
        break;
      case -1:
        LOG_ERROR("Heartbeat failed (no expiry). Error in SET: %s", app_name);
        return -1;
        break;
      default:
        LOG_DEBUG("TTL REPLY %s %lld", app_name, reply->integer);
        reply = redisCommand(GlobalApp.context,"GET %s", app_name);
        if (reply->type != REDIS_REPLY_INTEGER) {
          LOG_ERROR("TTL error, reply is not an integer.");
          return -1;
        } else {
          return reply->integer;
        }
    }
  }
  freeReplyObject(reply);
}

int start_app(char* app_name) {
  LOG_INFO("Starting app %s", app_name);
  char cmd[256];
  sprintf(cmd, APP_DIR"/%s &", app_name);
  int status = system(cmd);
  if (status != 0) {
    LOG_ERROR("Failed to start %s with exit code %d.", app_name, status / 256);
  }
  return(status/256);
}

int kill_app(char* app_name) {
  LOG_INFO("Killing processes with name %s", app_name);
  char cmd[128];
  sprintf(cmd, "killall %s", app_name);
  int status = system(cmd);
  if (status != 0) {
    LOG_ERROR("Failed to kill %s with exit code %d.", app_name, status / 256);
  }
  return (status/256);
}

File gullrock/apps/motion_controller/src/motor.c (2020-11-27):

#include <stdint.h>
#include <stdio.h>
#include <c-logger/logger.h>

#include "motor.h"


typedef void transition_func_t(MotorClass_t *motor);
typedef void run_func_t(MotorClass_t *motor);

void motorTransition(MotorClass_t *motor, motor_state_t new_state);
void motorRunState(MotorClass_t *motor);

void do_nothing(MotorClass_t *motor);
void do_idle_to_stopped(MotorClass_t *motor);
void do_idle_to_change_speed(MotorClass_t *motor);
void do_stopped_to_idle(MotorClass_t *motor);

transition_func_t * const transition_table[ MOTOR_NUM_STATES ][ MOTOR_NUM_STATES ] = {
    { do_nothing,         do_idle_to_stopped, do_idle_to_change_speed },
    { do_stopped_to_idle, do_nothing,         do_nothing },
    { do_nothing,         do_nothing,         do_nothing }
};

run_func_t * const run_table[ MOTOR_NUM_STATES ] = {
    do_nothing, do_nothing, do_nothing
};

void do_nothing(MotorClass_t *motor) {

}

void do_idle_to_stopped(MotorClass_t *motor) {
    
}

void do_idle_to_change_speed(MotorClass_t *motor) {
    
}

void do_stopped_to_idle(MotorClass_t *motor) {
    //check entry conditions
    LOG_INFO("entering idle");
    motor->state = MOTOR_STATE_IDLE;
}

int motorInit (MotorClass_t *motor) {
    motor->run = &motorRunState;
    motor->transition = &motorTransition;
    motor->state = MOTOR_STATE_STOPPED;
    return 0;
}

void motorTransition(MotorClass_t *motor, motor_state_t new_state) {
    transition_func_t *transition_fn = 
        transition_table[ motor->state ][ new_state ];

    transition_fn(motor);
}

void motorRunState(MotorClass_t *motor) {
    run_func_t *run_fn = run_table[ motor->state ];

    run_fn(motor);
}

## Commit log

2018-10-11 SQL functionality, sensor sim
    Working test on windows:
    - Simulates i2c read in thread
    - creates sql database
    - moved logger to config
    - test hook on merge (compile on arduino.ino change)
2018-10-12 Finalized SQL, modified utility fns, comm class
    - Improved SQL logic, archived file copy, working row addition
    - Made camera class (for start/stop recording)
    - Changed file structure
    - added i2c class to comm for write buffer
2018-10-12 removed print time
2018-10-13 Working RaspiCam stream and basic flask server Modified threads to allow for new camera thread per client Minor changes
2018-10-15 Working video and image save on socket.io message. Basic flask webpage with sockets + template file Bugs in sql.py ignored
2018-10-15 New gitignore to hold media folder structure New thread lock in comm.py - untested. To fix I/O error in sql - Continue: use Queue for var threads/SQL table? - More modular folder structures based on 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
2018-11-06 Improved thread management Made comm.py standalone for testing Working on i2c connection TODO: Arduino logic
2018-12-01 Maps, buttons, charts
    Map downloader, charts
2019-01-04 Major commit
    Haven't made a commit in a long time
    Too many changes to list particularily to:
    - WebGui and scoket io
    - sensor management
    - config file
    - dependencies
    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
2019-01-04 Improved logging
    Added logging framework configurable from config.ini
2019-02-02 Modified bus and sensors
    Changed schema
    Added self-tests
2019-02-03 Span object socket support
    Started map image system
2019-05-29 Bug fixes from raspberry pi test
2019-05-30 Arduino threaded read functionality
    Improved thread class to allow for locks
2019-06-13 BaseThread upgrades
    - Improvements to simply base threads
    - Added serial MCU thread
2020-11-25 Switch to submodules
2020-12-06 App updates (config and camera)
2020-12-11 working framework - threads and callbacks
2020-12-23 Internal sensors and arduino updates.
2021-01-22 Sensor and IO upgrades Fixed stack overflow bug, added watchdog
    [command_handler.cpp, def.cpp, def.h]
2021-01-25 V3 CAD files
    [4in_ABS_cap.SLDPRT, Assem1.SLDASM, M18 battery mount.SLDPRT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]
2021-02-12 Upload CAD files
    [MPC.kicad_pcb, MPC.sch, Naked Mega I-b.brd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]
2021-02-28 Add solidworks files
    [PiCam_WideAngle v2.step, Raspberry pi 3B+ model v10.step, assem_led.SLDASM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]

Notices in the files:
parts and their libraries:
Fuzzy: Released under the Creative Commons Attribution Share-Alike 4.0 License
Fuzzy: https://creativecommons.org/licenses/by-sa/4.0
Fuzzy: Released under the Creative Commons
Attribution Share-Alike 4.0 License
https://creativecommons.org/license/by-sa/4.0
